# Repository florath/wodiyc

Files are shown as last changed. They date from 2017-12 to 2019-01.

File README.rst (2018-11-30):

wodiyc
++++++

WOoden DIY CNC

python application to generate G-Code for a CNC machine.

*This project is unfinished.  Nevertheless some
parts are already useful.*

Introduction
============

During the years 2004 to 2006 some technical drawings of a wooden CNC
milling machine appeared in the Internet.  They were created by
someone called 'jgro'.  There are some versions of this machine and
it is still very popular - but it looks that nobody ever updated
the plans.

These plans had three major disadvantages:

#. All items and measures were given in inch.  Because I'm living in
   Europe, it is mostly impossible to get the items and tools to
   manufacture using the original plans.

#. A lot of 'additional' items are not available any longer.

#. The plans were not intended to be used in a CNC router itself.

Usage
=====

Checkout this project.

The file host_cnc.yaml contains the properties of the CNC machine
you are creating the GCode for.  Please adapt it to your needs.

The file wodiyc.yaml contains all the measurements of the CNC machine
to create (the target CNC machine). Adapt it as you want.

.. code:: bash

   python3 wodiyc/wodiyc_generate.py --wodiyc wodiyc.yaml --host-cnc host_cnc.yaml

After the run the subdirectory NGC contains the GCode files.

Requirements
============

A small list of requirements of this project:

#. Use metric measurements, items and tools

#. All items and tools should be available today and should be
   (somewhat) cheap.

#. The complete plans should be done in a way that they can be used
   in already build CNC milling machines to produce new ones.

#. The complete (software-) tool chain should be open source and
   available within the most common Linux distributions.

#. All parts are created with bridges.

The current toolchain is: python and linuxcnc.

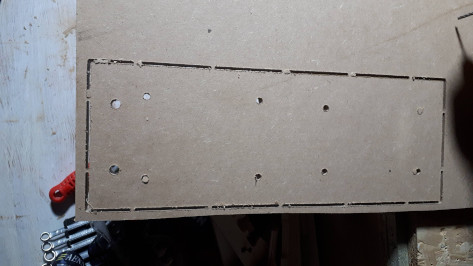
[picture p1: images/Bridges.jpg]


Parts
=====

This is the list of parts that already is available.

A complete list including images can be found in a separate Readme_.

.. _Readme: wodiyc/parts/Readme.rst

#. Adjustment Block: this is used for fixing the tubes and bearings.

#. Anti Backlash Nut

#. Reference: a small part to get the measurements correct

#. Support Bearing: used for manufacturing the linear bearings

#. Support: used for manufacuring parts with holes in the edge

#. ZAxis Bearing Support

#. ZAxis Linear Bearing

#. ZAxis Platform Back

#. ZAxis Platform Front

Notes
=====

Welcome to all who want to participate or improve.  Please just fork,
improve or change and send me a merge request.

Please note that I'm not a mechanics engineer.  All plans and the
generaded G-Code might contain errors and bugs.  Use them with care.

The license is chosen in a way that commercial use of the plans and of
course of any CNC milling machine is allowed.  But if you change the
plans you have also to publish the changes.

Status
======

This is not that important as this runs only pep8 and pylint.



Happy Milling.

Andreas Florath

andreas@florath.net

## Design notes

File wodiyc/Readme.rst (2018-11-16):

Results from first Reference
++++++++++++++++++++++++++++

Bridges are not equal distance on the backward stepping.
There is an offset of about +5mm for each bridge.

Pocket and cylinder (if not through) have a rough surface.
Idea: have another go for the deepest layer.

Measurements:

Tool Diameter: 3.175

is            should     %diff   description

71.0 - 71.5     70       102     overall x
50.9 - 51       50       102     overall y

50.3            50       101     pocket pos x
15              15       100     pocket pos y
9.4             10        94     pocket size x
29              30        96     pocket size y

9.4             10        94     cylinder radius x
9.0             10        90     cylinder radius y

14.3            15        95     notch radius x
13.8            15        92     notch radius y

5.7             6.2       92     screw radius x
5.3             6.2       85     screw radius y

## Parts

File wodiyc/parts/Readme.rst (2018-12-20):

Parts
+++++

AntiBacklashNut
===============
The anti backlash nut is self-made as I did not found any
for M12.  It is created using two blocks from aluminuim.  The picture
shows a raw one - without the thread.

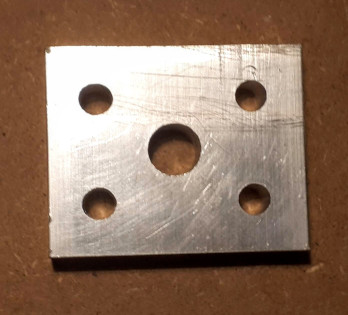
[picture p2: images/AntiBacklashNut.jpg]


The complet setup uses two of the nuts. The following image shows a
test-setup. In the machine later on one of the nuts is mounted
to the axis.  (Experiments with springs resulted in backslash
with higher forces.)

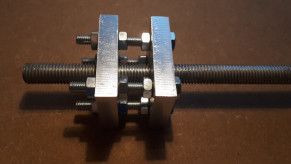
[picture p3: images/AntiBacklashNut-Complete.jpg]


Linear Bearing
==============
The linear bearings are the central concept of movement. They
are mounted on one side and role over the tubes on the other.

There are two sizes: the short for the Z axis and a longer one
for the X and Y axis.

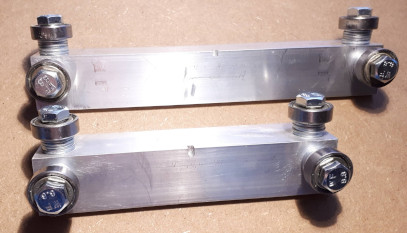
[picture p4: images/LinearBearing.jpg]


Reference
=========
This part is used only as measurement reference. It should
be created on the host CNC machine and all the measurements
should be checked.

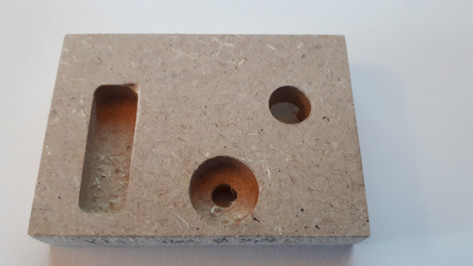
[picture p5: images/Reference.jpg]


SupportBearing
==============
This part is used for manufacturing the linear bearing.

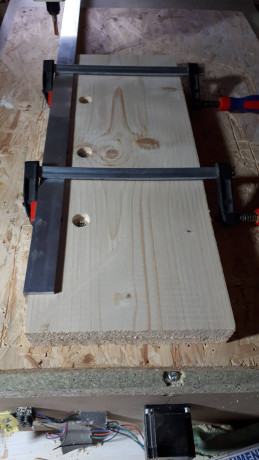
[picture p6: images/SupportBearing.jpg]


Support
=======
This is used for manufacuring other parts. It is fixed on the
CNC tables with M6 screws. Other parts can be fixed with clamps
to mill the edges.

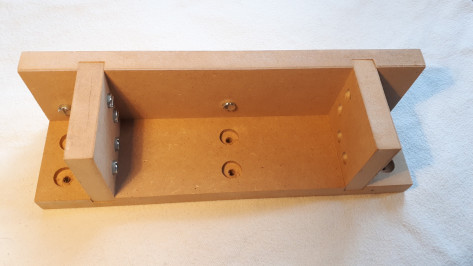
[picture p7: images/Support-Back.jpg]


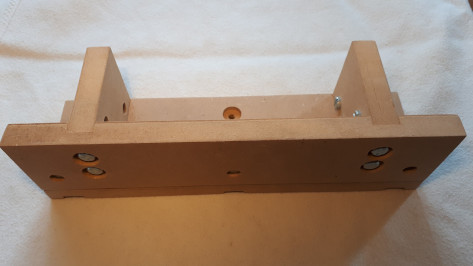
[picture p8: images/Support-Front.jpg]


ZAxisBearingSupport
===================
This part fixes the Z axis to the linear bearing.

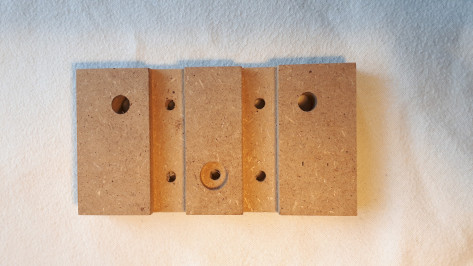
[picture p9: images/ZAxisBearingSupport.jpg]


ZAxisPlatform
=============
The tool is mounted here.

The original plan uses a 19mm MDF - which bends under a medium force.
Therefore the current approach uses two 16mm MDF plates glued together.







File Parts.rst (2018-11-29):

ZAxisLinearBearing-side
=======================

Place alu profile length to the Y-axis.  Fix it in this
direction (parallel to the Z-axis):

   AAAAAAAA
   AA
   AA
   AA
   AA

(0,0) is on the left bottom.

SupportBearing
==============
Use 40mm x 720mm wood. Use 8mm tool for cleaning surface.
Use 3.125mm tool for holes.
Place wood parallel to Y-axis.

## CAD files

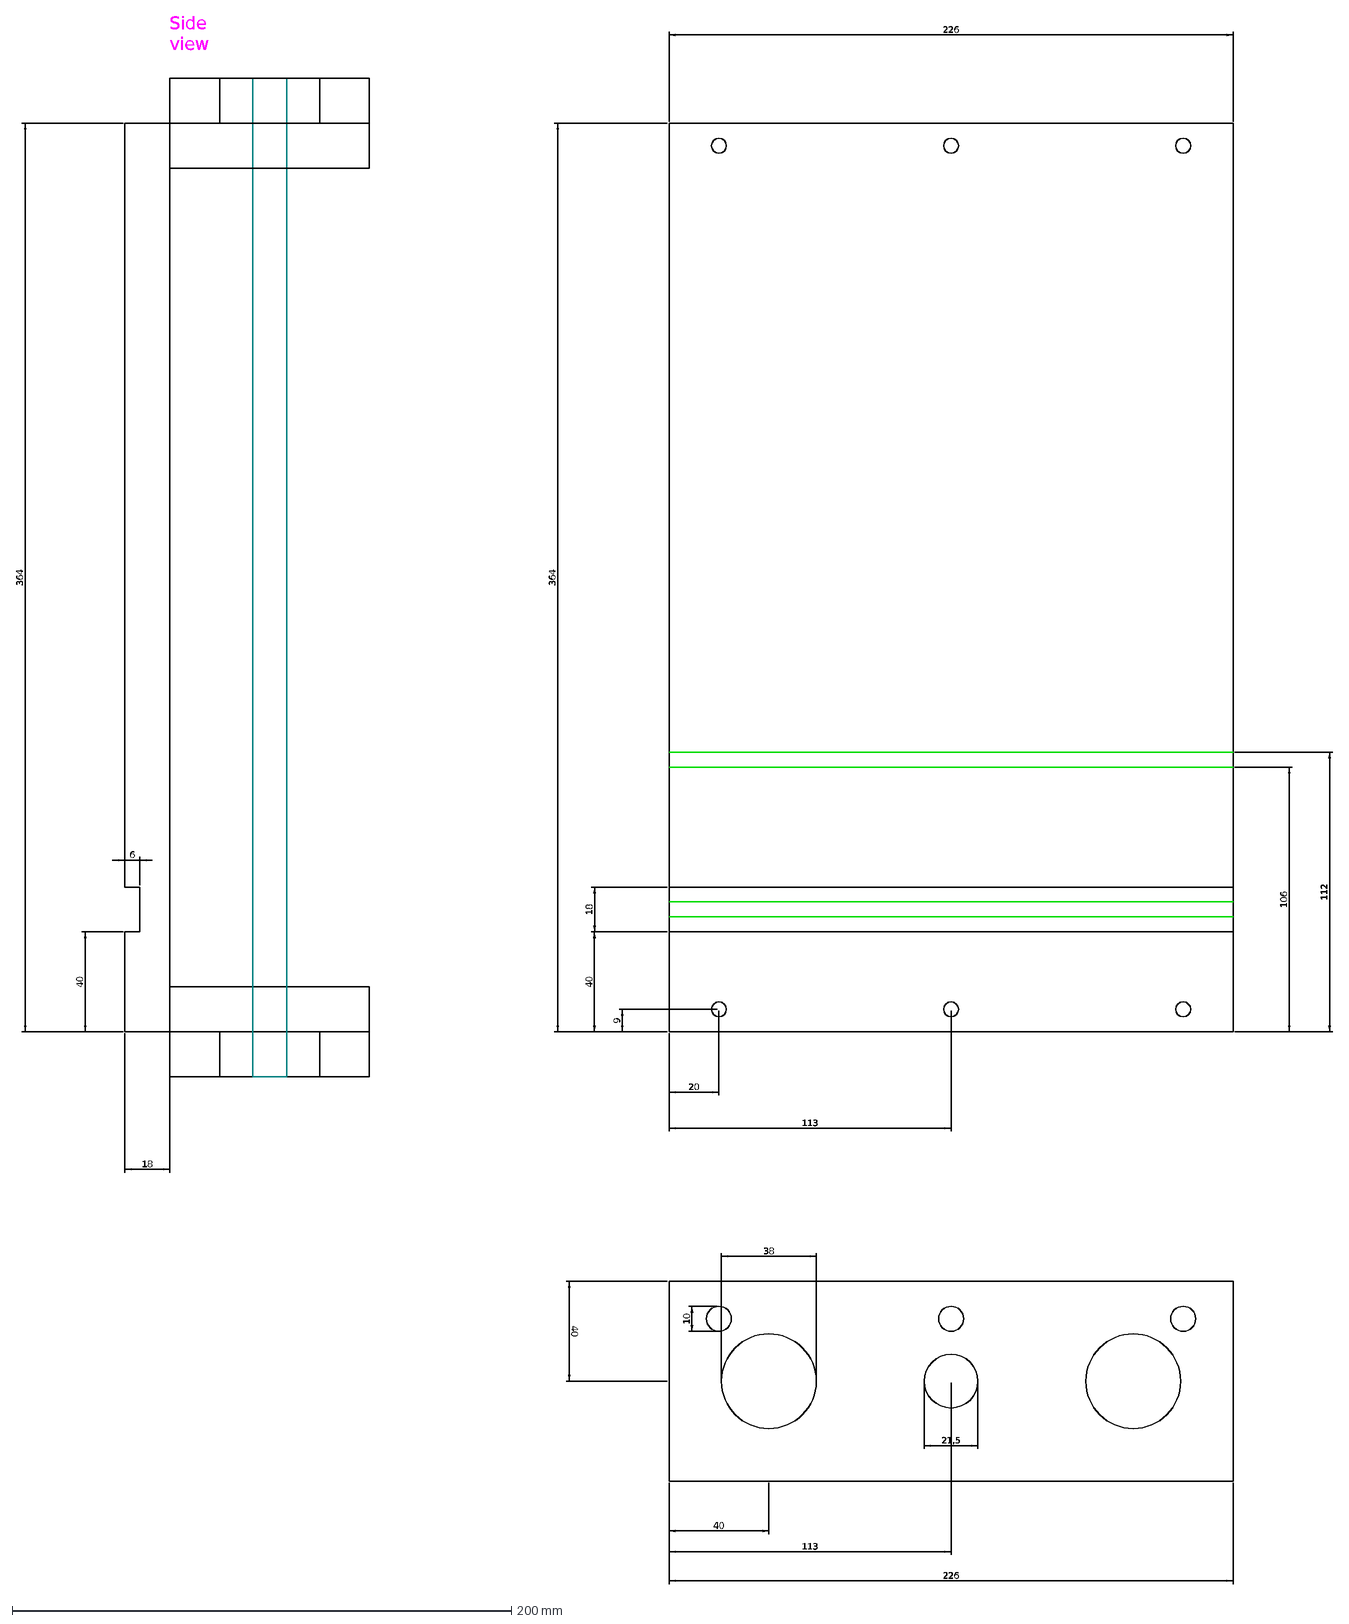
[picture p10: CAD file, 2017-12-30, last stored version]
plans/202_XAxis_Platform.dxf
364
Side view
226
18
40
6
106
112
20
113
9
38
21,5
10

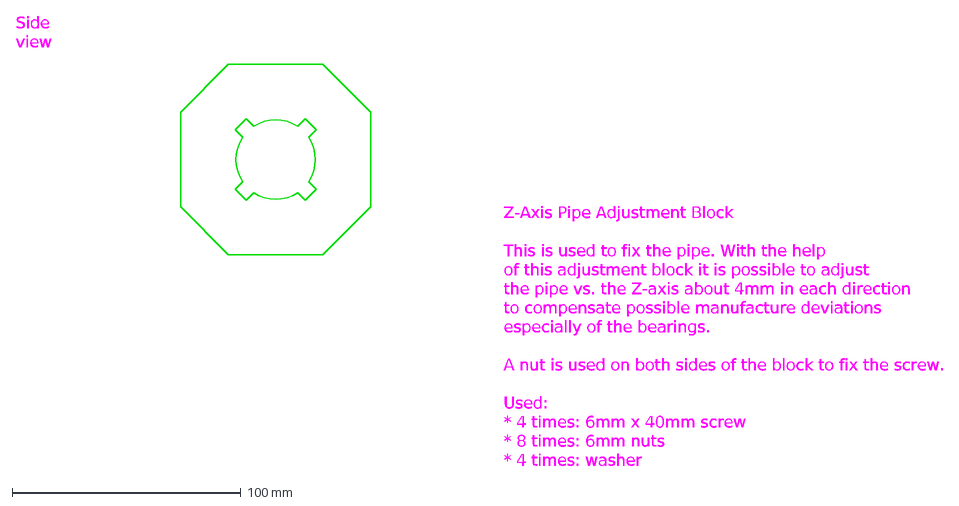
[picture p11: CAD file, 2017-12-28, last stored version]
plans/101_ZAxis_PipeAdjustmentBlock.dxf
Z-Axis Pipe Adjustment Block This is used to fix the pipe. With the help of this adjustment block it is possible to adjust the pipe vs. the Z-axis about 4mm in 
Side view

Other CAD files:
plans/102_ZAxis_Platform.dxf

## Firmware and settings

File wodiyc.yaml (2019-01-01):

---
# All measures in mm

# Global constants
distance_from_edge_small: &distance_from_edge_small 18

bearing_leg: &bearing_leg 30
bearing_thick: &bearing_thick 5

### Common and Global Constants

Common:
  # The base thickness of the MDF plates used for (mostly) all
  # construction
  base_material_thickness: &thickness 19
  # In reality the base material is sometime thicker.
  # For my current material at some points thickness of
  # 19.3 - 19.5 mm was measured - for a 19mm sheet.
  # The problem is, that at least at some positions (e.g.
  # cutouts) it is important to be really the correct size
  # if not - the parts do not fit.
  base_material_real_thickness: 20
  # For coutouts in the base material
  base_material_cutout_depth: &cutout_depth 6

  screwhole_diameter: &screwhole_diameter 6
  # This is choosen in the way that a 6mm screw can be fixed
  # using this notch.
  screwhole_notch_diameter: &screwhole_notch_diameter  15
  # This can be used for standard washers
  screwhole_notch_diameter_washer: &screwhole_notch_diameter_big  18.5
  # This is used to 'hide' the screw heads.
  screwhole_notch_depth: &screwhole_notch_depth  4
  # When only a small depth should be done - mostly to fit the washer
  screwhole_notch_depth_washer: 1

  threaded_rod_x_diameter: 12
  threaded_rod_y_diameter: 12
  threaded_rod_z_diameter: 12

  cross_nut_diameter: &cross_nut_diameter 10
  cross_nut_distance_from_edge: &distance_from_edge 25

  # This is a very central measurement:
  # it is the distance between the (central) pipe and the
  # elements around.
  # E.g. the adjustment blocks are sized in the way that
  # they use this measurement.
  pipe_distance: &pipe_distance 40

  # This is the security distance between moving parts.
  moving_parts_security_distance: &security_distance 5

  # Some parts need exact fit: because there is the need to
  # grind them, this is what is added to the original part
  grind_surcharge: 0.25

# ToDo: Rename Support -> Manufacuring
### Manufacuring

Support:
  x_size: &fix_x_size 270
  y_size: &fix_y_size  80
  z_size: &fix_z_size  16

  v_y_size: 60

  screwhole_diameter:           *screwhole_diameter
  screwhole_distance_from_edge: *distance_from_edge_small
  screwhole_distance_from_edge_small: 18
  screwhole_notch_diameter:     *screwhole_notch_diameter
  screwhole_notch_depth:        *screwhole_notch_depth

  v_screwhole_distance_from_edge:
  
  sleeve_diameter: 10.2
  sleeve_depth: 19

  cutout_depth: *cutout_depth
  cutout_distance: 180

  cross_nut_diameter: *cross_nut_diameter
  cross_nut_distance_from_edge: 18

  inner_cutout_offset: 3

SupportBearing:
  x_size: 200
  y_size: 720

  surface_clean_depth: 4
  # Added to all sides
  overlap: 4

  tool_surface: 2
  tool_holes: 1

  screwhole_diameter:           *screwhole_diameter
  screwhole_distance_from_edge: *distance_from_edge_small
  screwhole_notch_diameter:     *screwhole_notch_diameter
  # Extra depth - to have some tollerance towards the surface
  screwhole_notch_depth:        6

  fix_x_size: *fix_x_size
  fix_y_size: *fix_y_size
  fix_z_size: 14
  
  tool_change_depth: 2
  tool_change_diameter: 12

Reference:
  z_size: 12

### Adjustment Block

AdjustmentBlockBase:
  nut_cutoff: 6
  nut_indent: 2.5
  nut_height: 8
  nut_width: 10

AdjustmentBlock:

  half_size: *pipe_distance
  z_size: 19

  center_diameter: 36

  nut_width: 10
  nut_height: 8
  nut_indent: 2.5
  nut_cutoff: 6

  screwholes_diameter:             *screwhole_diameter
  screwholes_distance_from_corner: 19
  screwholes_notch_diameter:       18.5
  screwholes_notch_depth:          1

AdjustmentBlockBearing:
  screwholes_distance_from_corner: 14
  # The 12mm bearings have an outside diameter of 28mm
  center_diameter: 32
  size: 60

### Linear Bearing

LinearBearing:
  # There are two types of bearings: a short one and a lone one.
  # The short one is used for Z and X axis.
  length_x_axis: 150
  length_y_axis: 150
  length_z_axis: 200
  
  # ToDo: replace with above
  y_size_short: 150
  y_size_long: 200

  feed_rates: "alu_feed_rates"
  tool: 4
  tool_cleanup: 5

  # Because currently the tolerance of the CNC machine
  # is somewhat high, there is the need to add something
  # here to ensure that the hole is completely through.
  z_size: 5.2

  threadhole_diameter: 6.8
  # 11 mm is half of a bearing
  threadhole_distance_from_edge: 11
  threadhole_distance_from_top:  11

  # Latest after this depth a cleanup cycle is initiated
  cleanup_depth: 2

  # Number of times each operation is executed - to get
  # a better result.
  milling_times: 2

  # ToDo: This should be the reference!
  # OLD:
  bearing_leg: *bearing_leg
  # NEW:
  outer_leg_length: *bearing_leg

  # ToDo: This should be the reference!
  # NEW:
  thickness: 5

  # The offset over the edges when running cuts
  cut_offset: 7
  cut_depth: 4.75

  marker_x: 3
  marker_z: 3

### Anti Backlash Nut
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

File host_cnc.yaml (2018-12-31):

---
# The config used for cutting the machine itself
# This is the host config - where the wodiyc is build on

feed_rates:
  work: 900
  move: 1200
  dip: 100
free_movement: 10

alu_feed_rates:
  work: 200
  move: 1000
  dip: 50

tools:
  1:
    # The current tool (12pcs from China / 2 flutes)
    # cut only that far.
    diameter: 3.175
    hole_compensation: 0.75
    # difference / overlapping path when cutting
    diff: 2.5
    # This gives good results - for the costs of long
    # cutting times
    depth: 0.75
    finishing_runs: 10
  2:
    diameter: 7.5
    hole_compensation: 1.0
    # difference / overlapping path when cutting
    diff: 6
    # This gives good results - for the costs of long
    # cutting times
    depth: 2
    finishing_runs: 10
  3:
    # 90 degree
    diameter: 7.5
    hole_compensation: 1.0
    # difference / overlapping path when cutting
    diff: 1.5
    # This gives good results - for the costs of long
    # cutting times
    depth: 2
    finishing_runs: 10

  # For Alu
  4:
    diameter: 3.175
    hole_compensation: 0.1
    # difference / overlapping path when cutting
    diff: 2
    # This gives good results - for the costs of long
    # cutting times
    depth: 0.15
    finishing_runs: 10

  # Cleanup Tool Change
  5:
    diameter: 5
    hole_compensation: 0.1
    diff: 4
    depth: 0
    finishing_runs: 10

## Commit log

2017-12-28 Added hint about alpha stage of project
2017-12-28 Added X-Axis pipe adjustment block
    [101_ZAxis_PipeAdjustmentBlock.dxf]
2017-12-28 Added GCode for 101
    [101_ZAxis_PipeAdjustmentBlock.dxf]
2017-12-29 Added first version of X axis platform
    [202_XAxis_Platform.dxf]
2017-12-30 Added Z-axis platform plan
    [102_ZAxis_Platform.dxf, 202_XAxis_Platform.dxf]
2018-11-05 Using python and blender for darwing
    [101_ZAxis_PipeAdjustmentBlock.dxf, 102_ZAxis_Platform.dxf, 202_XAxis_Platform.dxf]
2018-11-10 Add Major Part of the Z Axis Platform front
2018-11-11 Fixed cylinder generation
2018-11-16 Fixed problems that occured during refactoring
    [wodiyc.yaml]
2018-11-18 Added travis
    [pylint.cfg]
2018-11-30 Added AntiBacklash nut photo
2018-12-02 Added Linear Bearing image
2018-12-03 Moved cylinder to native GCode
2018-12-03 Added image of backlash nut
2018-12-20 Adapted ZAxis Bearing Support
2018-12-22 Fixed ZAxisNutSupport and ZAxisBearingSupport
    [host_cnc.yaml, wodiyc.yaml]
2018-12-25 Refactor ZAxis Nut Support
2018-12-30 Added cleanup to cylinder
2018-12-31 Changed hole compensation of 1/8'' tool
2019-01-01 Add grind surplus to ZAxis Bearing support; add markers
